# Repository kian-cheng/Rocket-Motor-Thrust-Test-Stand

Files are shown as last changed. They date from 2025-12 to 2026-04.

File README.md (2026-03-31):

# Rocket-Motor-Thrust-Test-Stand
A rocket motor thrust test stand for commercial and experimental motors. 

Specification:
- Supports up to 45mm in diameter (potentially more tbh)
- Supports up to 200mm in length, but can be expanded
- Physical arming switch
- up to 80 Hz binary telemetry (as high as HX711 can be)
- Software arming
- Heartbeat + link-loss auto-disarm
- Single-shot ignition pulse

## Procedure (how to operate):
- Mount the rocket motor to the linear rail
- Get electronics set up (connect to ESP32)
- Ensure the end of the rocket motor sits flush with the loadcell plate without triggering
- Start logging and ignite!

## CAD:


## BOM:

2020 aluminium extrusion lengths:
- 2x 230mm
- 2x 110mm
- 1x 160mm
- 1x 20mm (for mounting load cell)

(optional, only needed for a dual orientation build)
- 2x 100mm
- 1x 150mm
- 2x 30mm

Electronics:
- ESP32
- HX711 + Loadcell (10kg or 20kg)
- IRLZ44N MOSFET
- Switch
- LEDs

Power can be supplied through a power bank or a combination of Li-ion cells with a buck-boost converter/LDO.

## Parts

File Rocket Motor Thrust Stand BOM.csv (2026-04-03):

Item | Description | Cost per pcs (USD) | Quantity | Total Cost | Link
110mm aluminium extrusion |  | 0.528 | 2 | 1.056 | https://shopee.com.my/product/197714890/7444516288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
150mm aluminium extrusion |  | 0.72 | 1 | 0.72 | https://shopee.com.my/product/197714890/7444516288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
100mm aluminium extrusion |  | 0.48 | 2 | 0.96 | https://shopee.com.my/product/197714890/7444516288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
30mm aluminium extrusion |  | 0.144 | 2 | 0.288 | https://shopee.com.my/product/197714890/7444516288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
230mm aluminium extrusion |  | 1.104 | 2 | 2.208 | https://shopee.com.my/product/197714890/7444516288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
160mm aluminium extrusion |  | 0.768 | 1 | 0.768 | https://shopee.com.my/product/197714890/7444516288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
Shipping |  | 1.32 | 1 | 1.32
Material Block | for machining the load cell mount | 11.4 | 1 | 11.4 | https://shopee.com.my/product/70248337/18194271855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
Li-Ion Battery | for powering esp32 | 2.74 | 1 | 2.74 | https://my.cytron.io/p-3.7v-2000mah-18650-li-ion-battery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
Linear Rail | MGN9H 200mm (300mm is shortest I could find, official Hiwin will have the correct size but would've costed 3 times more) | 15.37 | 1 | 15.37 | https://shopee.com.my/product/298182316/15324344938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
IRLZ44N | Ignition control | 2.26 | 2 | 4.52 | https://shopee.com.my/Original-IRLZ44N-IRLZ44-IRLZ44NPBF-IRLZ44A-N-Channel-Logic-Level-MOSFET-55V-49A-i.135112285.3002642939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
9V battery connector | For ignition | 0.1 | 1 | 0.1 | https://my.cytron.io/p-9v-battery-snap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
9V battery | For ignition | 3.27 | 1 | 3.27 | https://shopee.com.my/product/107050481/2297177678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
BMS | Battery charge and discharge | 0.69 | 1 | 0.69 | https://shopee.com.my/product/513412485/24919193465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

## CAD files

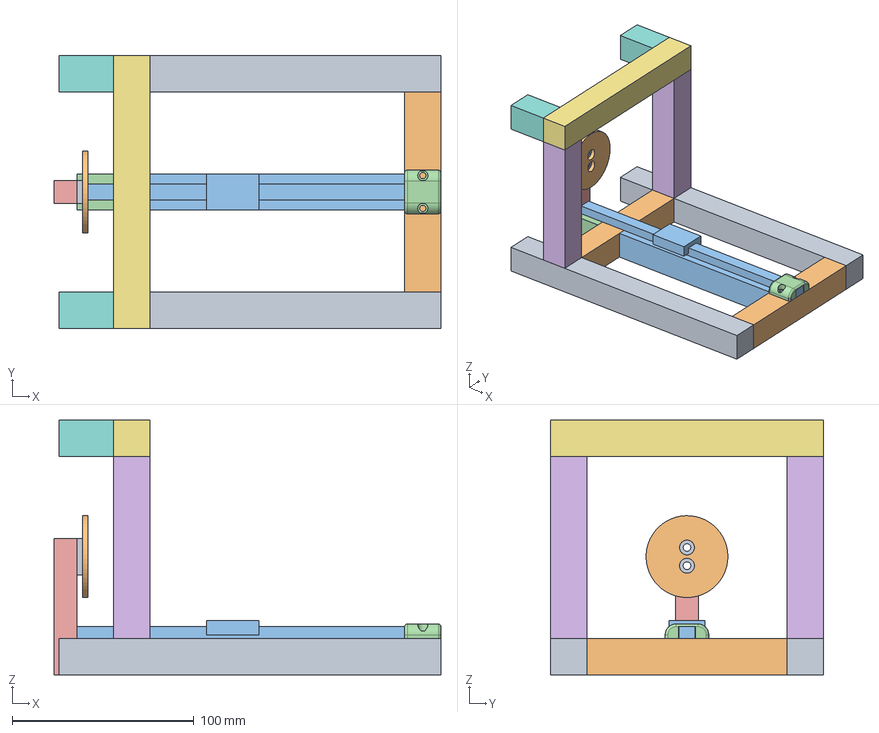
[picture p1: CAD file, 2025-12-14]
CAD/Rocket Motor Thrust Test Stand.step
212.7 x 150.0 x 140.0 mm

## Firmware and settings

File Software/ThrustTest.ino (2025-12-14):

#include <WiFi.h>
#include "HX711.h"

#define AP_SSID "IGNITION_TEST"
#define AP_PASS "fireee"

#define TCP_PORT 3333

#define HX711_DOUT 5
#define HX711_SCK  18
#define IGNITION_PIN   21
#define ARM_SWITCH_PIN 19   // physical arming switch 

WiFiServer server(TCP_PORT);
WiFiClient client;
HX711 scale;

bool softwareArmed = false;
bool ignitionActive = false;

unsigned long lastHeartbeat = 0;
unsigned long ignitionStart = 0;

const unsigned long HEARTBEAT_TIMEOUT = 1500;  // ms
const unsigned long IGNITION_PULSE_MS = 2000;   // ms
const unsigned long TELEMETRY_PERIOD  = 12;    // ~80 Hz

unsigned long lastTelemetry = 0;

//packet structure
struct TelemetryPacket {
  uint8_t  version;
  uint32_t time_ms;
  float    force;
  uint8_t  hw_armed;
  uint8_t  sw_armed;
  uint8_t  ignition;
  int8_t   rssi;
};

void setup() {
  Serial.begin(115200);

  pinMode(IGNITION_PIN, OUTPUT);
  digitalWrite(IGNITION_PIN, LOW);   // FAIL SAFE

  pinMode(ARM_SWITCH_PIN, INPUT_PULLUP);

  scale.begin(HX711_DOUT, HX711_SCK);
  scale.set_scale();   // calibrate later
  scale.tare();

  WiFi.mode(WIFI_AP);
  WiFi.softAP(AP_SSID, AP_PASS);

  Serial.print("AP IP: ");
  Serial.println(WiFi.softAPIP());

  server.begin();
}

void loop() {
  handleClient();
  handleHeartbeatTimeout();
  handleIgnitionPulse();
  sendTelemetry();
}

void handleClient() {
  if (!client || !client.connected()) {
    client = server.available();
    return;
  }

  while (client.available()) {
    String cmd = client.readStringUntil('\n');
    cmd.trim();

    if (cmd == "HB") {
      lastHeartbeat = millis();
    }

    else if (cmd == "ARM") {
      softwareArmed = true;
    }

    else if (cmd == "DISARM") {
      softwareArmed = false;
      ignitionActive = false;
      digitalWrite(IGNITION_PIN, LOW);
    }

    else if (cmd == "FIRE") {
      if (ignitionAllowed() && !ignitionActive) {
        ignitionActive = true;
        ignitionStart = millis();
        digitalWrite(IGNITION_PIN, HIGH);
      }
    }
  }
}

bool ignitionAllowed() {
  bool hwArmed = digitalRead(ARM_SWITCH_PIN) == LOW;
  return hwArmed && softwareArmed;
}

void handleHeartbeatTimeout() {
  if (millis() - lastHeartbeat > HEARTBEAT_TIMEOUT) {
    softwareArmed = false;
  }
}

void handleIgnitionPulse() {
  if (ignitionActive && millis() - ignitionStart >= IGNITION_PULSE_MS) {
    ignitionActive = false;
    digitalWrite(IGNITION_PIN, LOW);
  }
}

void sendTelemetry() {
  if (!client || !client.connected()) return;
  if (millis() - lastTelemetry < TELEMETRY_PERIOD) return;

  lastTelemetry = millis();

  TelemetryPacket pkt;
  pkt.version  = 1;
  pkt.time_ms  = millis();
  pkt.force    = scale.get_units(1);
  pkt.hw_armed = digitalRead(ARM_SWITCH_PIN) == LOW;
  pkt.sw_armed = softwareArmed;
  pkt.ignition = ignitionActive;
  pkt.rssi     = WiFi.RSSI();

  client.write((uint8_t*)&pkt, sizeof(pkt));
}

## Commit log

2025-12-14 Revise README for thrust test stand specifications
    Updated the description and specifications of the rocket motor thrust test stand.
2025-12-14 Update README with BOM and specifications
    Added Bill of Materials (BOM) section with specifications for aluminium extrusion lengths and electronics.
2026-03-09 Update Rocket Motor Thrust Stand BOM with new items
    [Rocket Motor Thrust Stand BOM.csv]
2026-04-03 Update Rocket Motor Thrust Stand BOM.csv
    [Rocket Motor Thrust Stand BOM.csv]
